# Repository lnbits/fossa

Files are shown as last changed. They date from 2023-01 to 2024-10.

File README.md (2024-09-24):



Welcome to the FOSSA project! FOSSA is an innovative, open-source Bitcoin Lightning ATM designed to be cost-effective and easy to build. Utilizing standard components such as an ESP32 microcontroller, a multi-coin acceptor, and a bill acceptor, FOSSA allows anyone to convert loose fiat change into Bitcoin efficiently. The project includes comprehensive instructions and resources, making it accessible for hobbyists and developers to create a fully functional Bitcoin ATM. Dive in and get started building your own FOSSA!

## Demo

https://twitter.com/arcbtc/status/1567639231333277697

## Bill of Materials

The parts for this ATM should be approximately £200-£250!

You can run the FOSSA as a coin machine, a bill acceptor, or both.

### Primary FOSSA components

| Part | Description | Buy (UK) | Estimated cost |
|---|---|---|---|
| ESP32 WT32-SC01 | This is the ESP32 touchscreen. You don't need any Wi-Fi. It should be supplied with a USB-C to USB cable. Note that the ESP32 WT32-SC01 is different from the ESP32 WT32-SC01 PLUS! | Ebay or [AliExpress](https://www.aliexpress.com/item/1005003191471709.html) | **£45** |
| Option: NV10USB+ bill acceptor | The bill acceptor option to accept cash notes. To accept GBP, you should request that it be set to GBP and SIO mode when purchasing. | [Ebay (second hand)](https://www.ebay.co.uk/itm/263398460026) | **£70-£150** |
| Option: DG600F(S) Multi Coin Acceptor | The coin acceptor option. The "S" denotes the front panel (stainless steel sheet version, where we can 3D print a black panel for it). | [AliExpress](https://www.aliexpress.com/w/wholesale-DG600F(S)-Multi-Coin-Acceptor.html?spm=a2g0o.home.search.0) or eBay | **£30** |
| Screw terminal block | Easily connect the wires without soldering. | [Amazon (UK)](https://www.amazon.co.uk/gp/product/B08LNWMMHQ) | **£1** |
| 12v power supply | Best to get one with terminal block adapter (12v battery also works well, for unplugged version). | [Amazon (UK)](https://www.amazon.co.uk/gp/product/B09MTBTXDJ/) | **£8** |
| 12v to 5v step down converter with USB | 12V to 5V: The adapter converter module can convert unstable voltage DC 12V to stable DC 5V / 15W 3A output. | [Amazon (UK)](https://www.amazon.co.uk/gp/product/B07QQ587K3) | **£5**
| Male-to-female GPIO jumpers | Plug and play GPIO connectors | [Amazon (UK)](https://www.amazon.co.uk/gp/product/B09MJZDXBB) | **£5**
| Option: Aluminum "medicine box" | Cheap medicine box for the cash machine | Amazon (UK) | **£30** |
| Option: Amazon Basic Home Safe | More secure box | Amazon (UK) | **£70** |
| Option: 58mm 701 USB Thermal Receipt Printer | Print receipts for users. **NB The 3D printed enclosure does not currently fit this**. | [Ebay (UK)](https://www.ebay.co.uk/itm/293668439213) | **£25** |



### 3D printed enclosure fixtures & fittings

For the 3D-printed version, you will need:

| Part | Description | Buy (UK) |
|---|---|---|
| M4 x 16mm pan head security torx tamper-resistant bolts | These hold the front facia to the back box. Anything longer than 14mm - 55mm is fine. | [Amazon (UK)](https://www.amazon.co.uk/gp/product/B0BTTRPBQV/) |
| Tamper-proof torx wrench (T20) | To tighten the front facia Torx bolts. | [Amazon (UK)](https://www.amazon.co.uk/gp/product/B0D53LNNRW) |
| Brass insert nuts, M4 x 6mm L x 6mm OD | Female threaded heat set knurled embedded insert nuts for 3D printing. These are stronger than trying to create threads in the 3D print. Using a soldering iron, these are heated up and pushed into the backbox for better attachment of the facia. | [Amazon (UK)](https://www.amazon.co.uk/gp/product/B09MCVW4GQ/) |
| M4 x 30mm carriage/coach bolts | These are to replace the bolts supplied with the coin acceptor to accommodate the thickness of the facia. | [eBay (UK)](https://www.ebay.co.uk/itm/386550912089?var=653926055961) |
| 5.5mm x 2.1mm DC Power Jack Socket Female Panel Mount Connector | This allows the 12V adaptor to plug into the ATM's outside. The box assumes a diameter of 7.7mm (like these). | [Amazon (UK)](https://www.amazon.co.uk/dp/B01N3679B8) |
| 2.2mm Quick Disconnect Female Spade Connector | This allows us to crimp a cable and connect to the 5.5mm x 2.1mm DC Power Jack Socket | |
| Cabinet draw tubular 16mm lock | This will be mounted on the door. | [Amazon (UK)](https://www.amazon.co.uk/Litensh-Tubular-Cylinder-Cupboard-Letterbox/dp/B09SHWXWXC/) |
| Optional: Rubber feet (D30x22xH15) | If you want to have this one on the table, some rubber feet will go at the bottom of the backbox with an M5 bolt. You can also use adhesive versions. Grooves in the bottom of the box will support up to 30mm in diameter. | [Amazon (UK)](https://www.amazon.co.uk/dp/B0CQ23M5Z5) |
| Optional: M5 x 16mm hex socket bolts | To screw the rubber feet into the back box. | [Amazon (UK)](https://www.amazon.co.uk/16mm-Socket-Button-Head-Screws/dp/B09BG8XNM7) |
| Optional: M5 nylon nuts | To screw the rubber feet into the backbox. | [Amazon (UK)](https://www.amazon.co.uk/Bolt-Base-Stainless-Insert-Nylock) |
| Optional: Adhesive security plate and locking cable | Secure the ATM when desk mounted. | [Amazon (UK)](https://www.amazon.co.uk/I3C-Security-Anti-Theft-Hardware-Smartphone/dp/B07FM93JL6) |

## Build

A video tutorial is available here on how to construct the FOSSA:

[https://www.youtube.com/watch?v=vbyYb9Yiu_k](https://www.youtube.com/watch?v=vbyYb9Yiu_k)

### Step 1: Hardware Setup

> **STAY TUNED FOR A WIRING HARNESS TO MAKE THIS PLUG-AND-PLAY, AND YOU CAN SKIP TO STEP 2.**

This method requires no soldering. We do this by using GPIO jumpers and terminal blocks. First, split a terminal block into a block of 3 (our LIVE terminal) and a block of 4 (our GROUND terminal).

The wiring reference is as follows:



**To connect the bill acceptor**:

1. Connect the Rx (GPIO 32) and Tx (GPIO 33), pins 29 and 31, on the WT32-SC01 board to pins 1 and 5, respectively, on the bill acceptor.
2. Using a GPIO jumper, connect the live wire (pin 15) to the first LIVE terminal block at an available terminal.
3. Using a GPIO jumper, connect the ground wire (pin 16) to a second GROUND terminal block of block at an available terminal.
4. Connect the positive wire (red) of the 12V to 5V power converter and connect it to the LIVE terminal block at an available terminal.
5. Connect the negative wire (black) of the 12V to 5V power converter and connect it to the GROUND terminal block at an available terminal.
6. Connect the ground pin (e.g. pin 5) of the WT32-SC01 and connect it to the 2nd terminal of the GROUND terminal block at an available terminal.

| NV10USB+ Pin | WT32-SC01 Pin No. (Not GPIO No.) | Power Supply |
|---|---|---|
| 1 (Tx)  | 31 | N/A |
| 5 (Rx)  | 29 | N/A |
| 15 (12V DC+) | N/A | 12V DC+ |
| 16 (GND) | 5 | GND |

> The bill acceptor needs to be programmed to your currency and set to `SIO` mode. Usually, you can buy them preconfigured. If you have to program, buy <a href="https://www.innovative-technology.com/shop/cables/nv9-nv10-usb-host-cable-detail">this wire</a> and download the Validator Manager software <a href="https://www.dropbox.com/sh/2mle0czl2j2w7yq/AABie6AJQTq-tXmBv1TUhBUGa?dl=0">here</a> or <a href="http://www.innovative-technology.com/support/secure-download">here</a> (sadly only runs on windows, so use a friends machine). Details on programming can be found <a href="https://github.com/arcbtc/fossa/blob/main/NV10Manual_2.PDF.pdf">here</a>. It's relatively straightforward to program the acceptor: plug in the USB host cable, turn it on by holding the config button for 2 seconds, and open the Validator Manager software. If you prefer to build your own programming cable, see page 42 of the <a href="NV10 operations manual.pdf">NV10 USB Operations Manual</a>, which gives a wiring diagram for the NV10 USB host cable. You can ignore all the hardware requirements for programming in the guide; you just need the host cable! Don't try using the programming cards in the guide; that's an old system these machines no longer support - "Many Bothans died to bring us this information"!

**To connect the coin acceptor**:

> NB You can usually order the coin acceptor pre-programmed to your currencies. Otherwise, you will need to train the acceptor using <a href="https://www.youtube.com/watch?v=Dyun1xjKqc4">this guide</a>.

1. Set the 3rd dip switch to high (this sends integers to the WT32-SC01 rather than pulses).
2. Using a GPIO jumper, connect the interrupt pin (pin 5) on the coin accepter to the 5V pin (pin 2) on the WT32-SC01.
3. Using a GPIO jumper, connect the serial out (pin 2) on the coin accepter to pin 4 on the  WT32-SC01.
4. Using a GPIO jumper, connect the live pin (pin 1) to the LIVE terminal block at an available terminal.
5. Using a GPIO jumper, connect the GND pin (pin 3) on the coin accepter to the GROUND terminal block at an available terminal.

| DG600F(S) Pin | WT32-SC01 Pin No. (Not GPIO No.) | Power Supply
| --- | --- | --- |
| 5 | 2 | N/A |
| 4 | N/A | N/A |
| 3 (GND) | N/A | GROUND
| 2 (serial out) | 4 | N/A
| 1 (12V) | N/A | LIVE

**To connect the 12V power supply**:

1. Connect a GPIO jumper to the live connection (+) on the 12V power supply terminal block adapter to the LIVE terminal block at an available terminal.
2. Connect a GPIO jumper to the ground connection (-) on the 12V power supply terminal block adapter to the GROUND terminal block at an available terminal.

**To complete the terminal blocks**:

1. Connect each terminal in the LIVE terminal block so they all receive power by looping over wires from terminals 1 to 2 and 1 to 3.
2. Connect each terminal in the GROUND terminal block so they all receive power by looping over wires from terminals 1 to 2, 1 to 3 and 1 to 4.

**To connect to power**:

1. Plug in the WT32-SC01 to the USB connector of the 12V to 5V power converter.
2. Plug in the connection terminal of the 12V power supply and connect to mains power.

You should hear the bill acceptor and coin acceptors turn on.

### Step 2: Configure LNBits

To configure your LNBits instance to pull funds from:

1. Login to your instance of LNBits.
2. Create a wallet.
3. Go to `Manage Extensions`, find `LNURLDevice`, and install/enable it.
4. Open the `LNURLDevice` extension, click `New LNURLDevice Instance`, give it the title of `ATM`, and choose the appropriate wallet for the ATM. Select the correct currency (e.g., `GBP`), `ATM` mode, and a percentage for the commission.
5. Copy the link it gives you.

### Step 3: Programming the WT32-SC01

The ATM is configured in two parts: the ATM and LNBits running on a separate node.

To set up your Arduino IDE:

1. If you have not already done so, install the Arduino IDE from [https://www.arduino.cc/en/Main/Software](https://www.arduino.cc/en/Main/Software).
2. Install the ESP32 libraries. You can do this by copying the stable release version link, currently `https://espressif.github.io/arduino-esp32/package_esp32_index.json` and putting in the `File` > `Preferences...` > `Additional Board Manager URLs` (see: [https://docs.espressif.com/projects/arduino-esp32/en/latest/installing.html](https://docs.espressif.com/projects/arduino-esp32/en/latest/installing.html))
3. Install the boards by going to `Tools` > `Board` > `Board Manager...`, searching for ESP32, choose 2.0.17, and click Install.
4. Copy the libraries from this project <a href="/libraries">libraries</a> folder to your `"/Arduino/libraries"` folder (usually in OS `"Home"` directory)
5. Clone the repo and open accessPointFOSSA.
6. Select the relevant port and ESP32 dev module.
7. Go to `Sketch` > `Upload`.
8. Once uploaded, the access portal will launch when you press the screen on the WT32-SC01 device.

To configure the ATM:

1. Connect the access portal wi-fi (`Device-fa7ce5a4`, for example).
2. Open the access portal.
2. Enter a new password.
3. Enter the coin denominations (if you are using a coin acceptor, separated by a comma)
4. Enter the maximum withdrawal amount in fiat (e.g. `30` for 30 GBP).
5. Enter a percentage charge for the service (e.g. `10` for 10%, which should be the same value you entered into LNBits).
6. Click `Save`.
7. unplug and plug the WT32-SC01 back in once saved. You should see the `Fiat for Sats` screen.

### Step 4: Enclosure

> It should be pointed out that this ATM is designed to be attended to (such as on a shop counter) rather than something that can be left unattended and mounted to a wall.

#### Option A: 3D printed enclosure

If you want to want to print your own enclosure, we recommend these settings:

1. Print the Facia
    - STL: [FOSSA ATM Facia](https://github.com/lnbits/fossa/blob/main/3DPrints/FOSSA%20ATM%20Facia.stl)
    - Material: PETG
    - Layer: 0.2mm
    - Infill: 10-100% (recommend 20%+)
    - Supports: Yes
    - Notes: To set the Bitcoin logo with a different color, set a color change at layer 114 (13.20mm). In PrucaSlicer, you can "paint" out all the screw holes as they do not need supports. I would also recommend setting a thicker layer parameter, in PrucaSlicer, you can do this by settings `Printer Settings` > `Layers and perimeters` > `Perimeters` to `4`)
3. Print the backbox
    - STL: [FOSSA ATM Backbox](https://github.com/lnbits/fossa/blob/main/3DPrints/FOSSA%20ATM%20Back%20Box.stl)  
    - Material: PETG
    - Layer: 0.2mm 
    - Infill: 10-100% (recommend 20%+)
    - Supports: Yes
    - Notes: In PrusaSlicer you can set `Print Settings` > `Support material` > `First layer expansion` to `1 mm`, `XY separation between an object and its support` to `80%` and `Overhang threshold` to `1 mm`, or, you can "paint" out all but the door as the model has been designed for minimal supports
4. Print the accessories
    - STL: [FOSSA ATM WT-32-SC01 Backplate](https://github.com/lnbits/fossa/blob/main/3DPrints/FOSSA%20ATM%20WT-32-SC01%20Backplate.stl), [FOSSA ATM Coin Slot Cover](https://github.com/lnbits/fossa/blob/main/3DPrints/FOSSA%20ATM%20Coin%20Slot%20Cover.stl), [FOSSA ATM 4mm Lock Lever Shim](https://github.com/lnbits/fossa/blob/main/3DPrints/FOSSA%20ATM%204mm%20Lock%20Lever%20Shim.stl), [FOSSA ATM Door](https://github.com/lnbits/fossa/blob/main/3DPrints/FOSSA%20ATM%204mm%20Door.stl), [FOSSA ATM Backbox Note Holder](https://github.com/lnbits/fossa/blob/main/3DPrints/FOSSA%20ATM%20Backbox%20Note%20Holder.stl)
    - Material: PETG
    - Layer: 0.2mm 
    - Infill: 10-100% (recommend 20%+)
    - Supports: No
5. Use a soldering iron to melt the brass female embedded insert nuts into the six holes for the facia (see picture 1 below)
6. OPTIONAL: If using the coin acceptor, replace the coach bolts with longer bolts (M4 x 30mm carriage/coach bolts) to account for the thickness of the facia.
7. Mount the bill acceptor so it is "smiling" (see picture 2) with the supplied mounting bracket and screws as pictured (see picture 3). You can remove the bill input feed from the main part of the unit and then re-attach it.
8. Mount the screen to the WT-32-SC01 Backplate.
9. Mount the backplate to the Facia with the M4 (4mm x 8mm Inc Head) hex socket countersunk screws.
10. Mount the backbox note holder to the backbox with the M4 (4mm x 8mm Inc Head) hex socket countersunk screws.
11. Mount the 5.5mm x 2.1mm DC Power Jack Socket Female Panel Mount Connector in the hole in the back left of the backbox (this directs the notes to the bottom of the box.
12. Connect wires from the connection terminal to the 2.2mm Quick Disconnect Female Spade Connector and plug into the inside of the 5.5mm x 2.1mm DC Power Jack Socket Female Panel Mount Connector.
13. OPTIONAL: Mount the Rubber feet (D30x22xH15) using the M5 x 16mm hex socket bolts and M5 nylon nuts (be careful not to over-tighten).
14. Using the Tamper-proof torx wrench (T20), use the screw in the M4 x 16mm pan head security torx tamper-resistant bolts to secure the facia to the backbox.
15. Plug the power supply in.





#### Option B: Mount in a box

Use the templates provided <a href="cuttingTemplate.pdf">here</a>, print out at 100% on standard UK A4, and check the dimensions are correct after printing. It's helpful if the bill acceptor and coin mech pins are accessible.

* For the `Aluminium Storage Box` solution, holes can be cut with a sharp knife (clearly not secure - but acceptable for somewhere you can keep an eye on the ATM or for demos).

* For the `Home Safe` solution, holes can be cut with an angle grinder and a very thin cutter. (If you have not used an angle grinder before, don't be scared; they're cheap, easy enough to use, and very useful. Take your time and wear safety equipment.)

> We use CT1 sealant/adhesive (or similar) for mounting the screen, although the screen has screw points, which should prob be used for added security.

## Get in touch

And there you have it. Have fun, and tag us on Twitter / Nostr with all your cool setups!

> <i>Join our <a href="https://t.me/makerbits">telegram support/chat</a>.</i>

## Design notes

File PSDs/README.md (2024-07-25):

## PhotoShop Files

### FOSSA - The FOSS ATM

This is the heading image for the repo.

### FOSSA - Primary components

Overview visual of the main components used.

### FOSSA - Primary wiring reference

Wiring and pin labelling for the main components.

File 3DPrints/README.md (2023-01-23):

##### Few people have used a case for the WT32, this does however add the security risk that people have access to the USB. A flush finish and not using a case is advised, but we thought we'd share anyway.

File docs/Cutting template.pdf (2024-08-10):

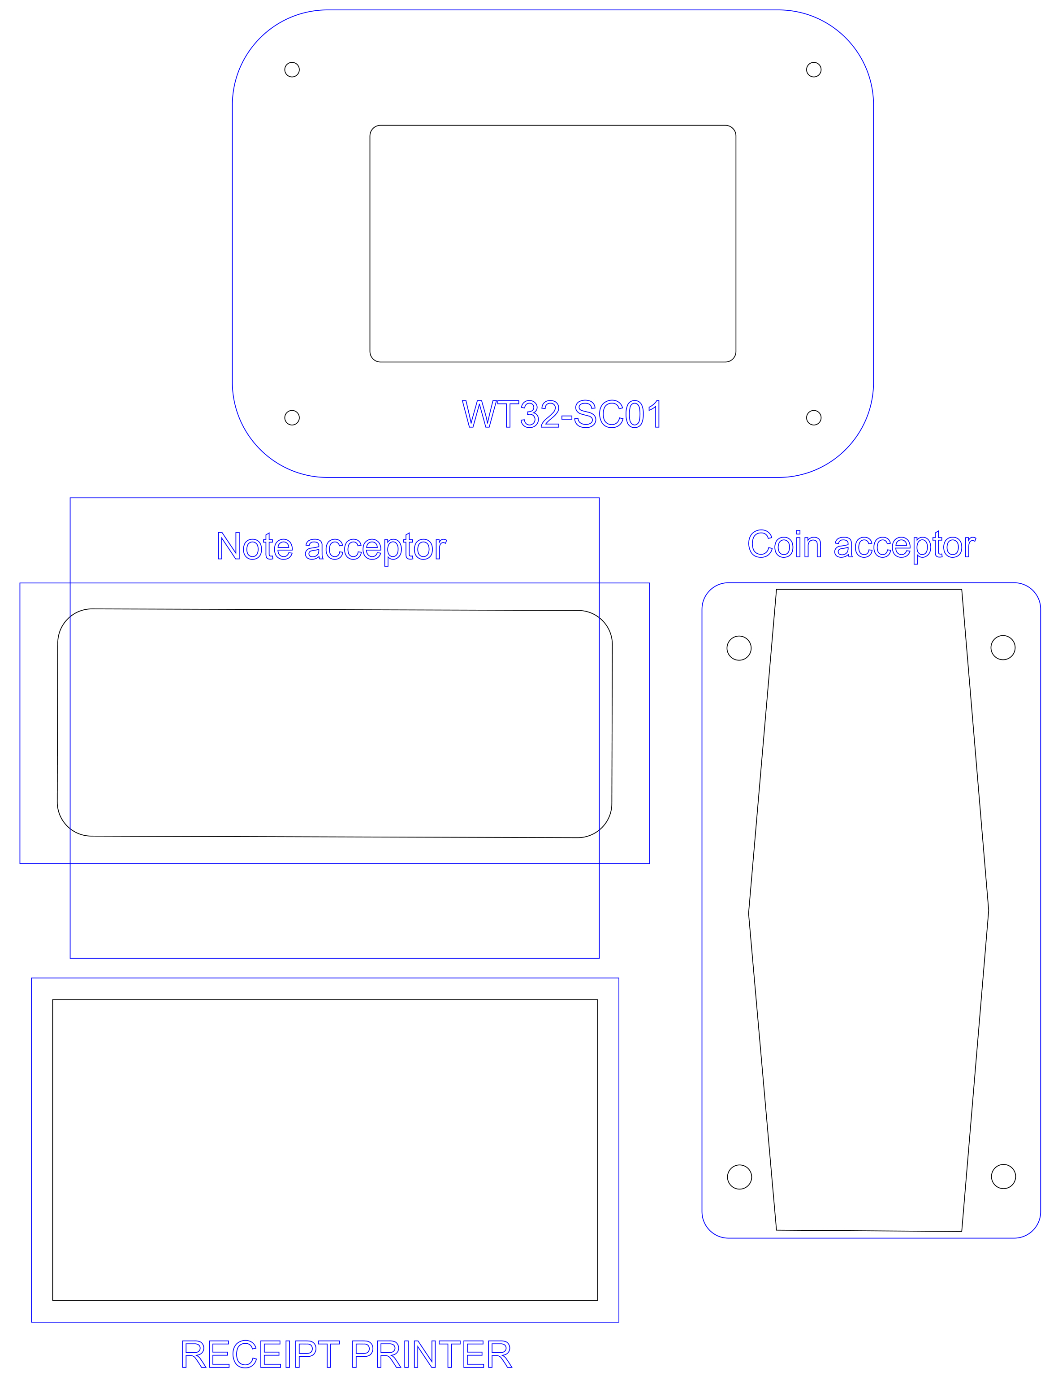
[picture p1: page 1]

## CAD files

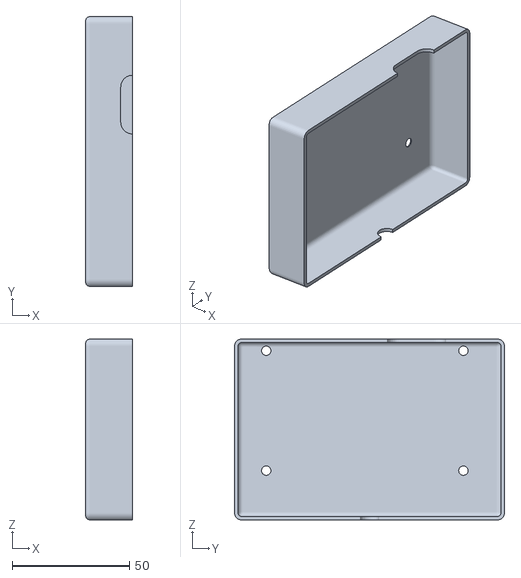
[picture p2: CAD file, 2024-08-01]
3DPrints/FOSSA ATM LNBits Board Cover.stl
20.0 x 114.9 x 77.0

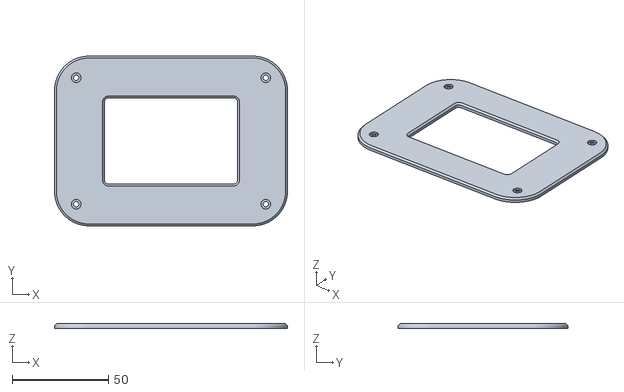
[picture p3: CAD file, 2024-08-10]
stls/WT32-SC01 enclosure upper.stl
121.2 x 88.3 x 2.50

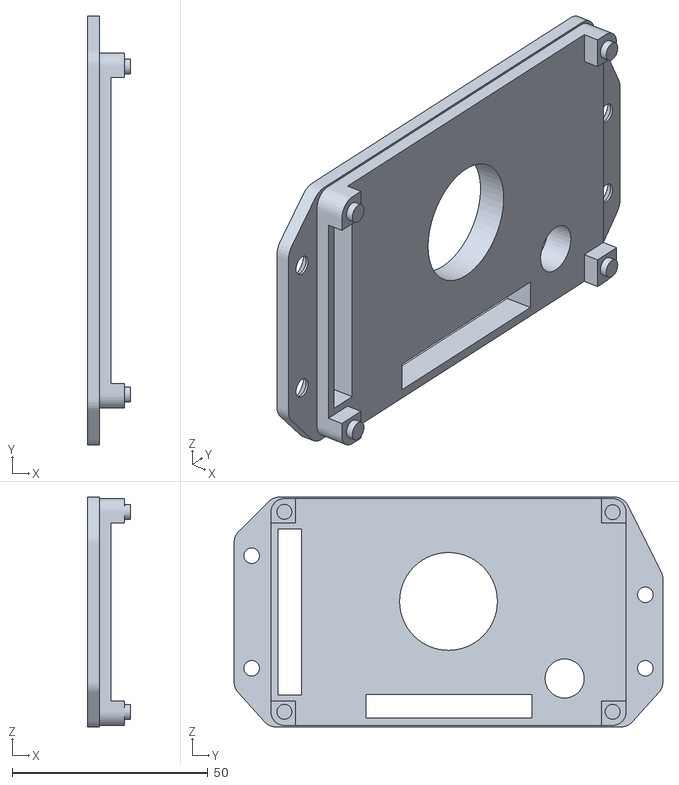
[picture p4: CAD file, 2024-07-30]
3DPrints/FOSSA ATM WT32-SC01 Backplate.stl
10.9 x 109.7 x 58.8

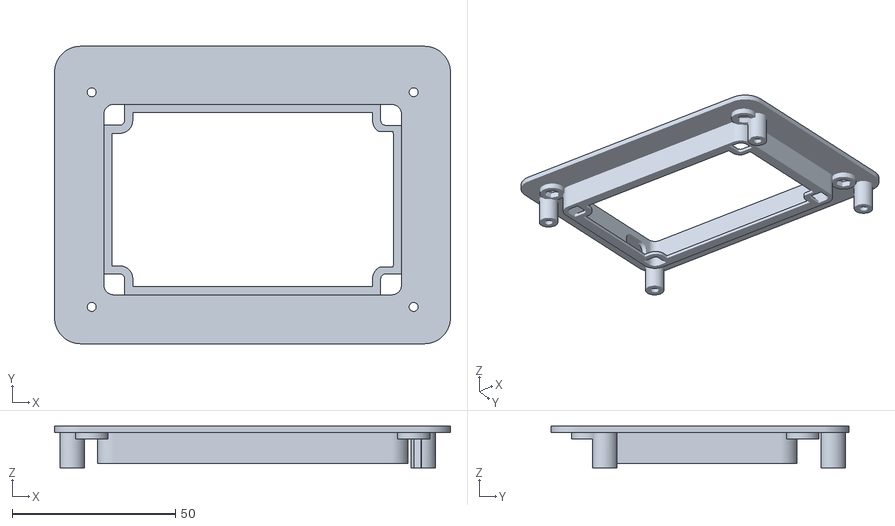
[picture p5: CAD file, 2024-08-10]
stls/WT32-SC01 enclosure lower.stl
121.3 x 91.1 x 12.8

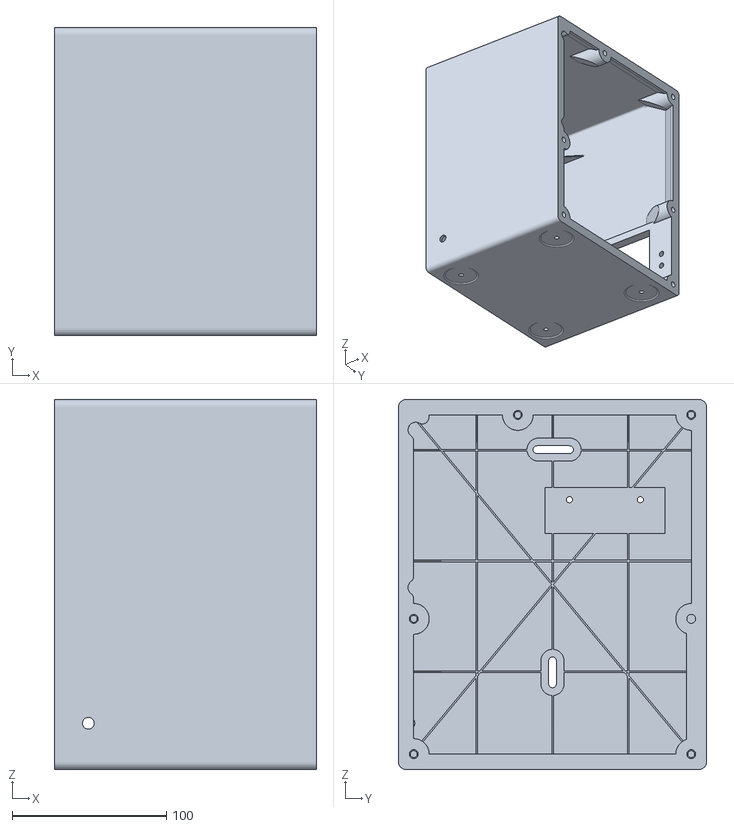
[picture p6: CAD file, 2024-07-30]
3DPrints/FOSSA ATM Backbox.stl
170.0 x 200.0 x 240.0

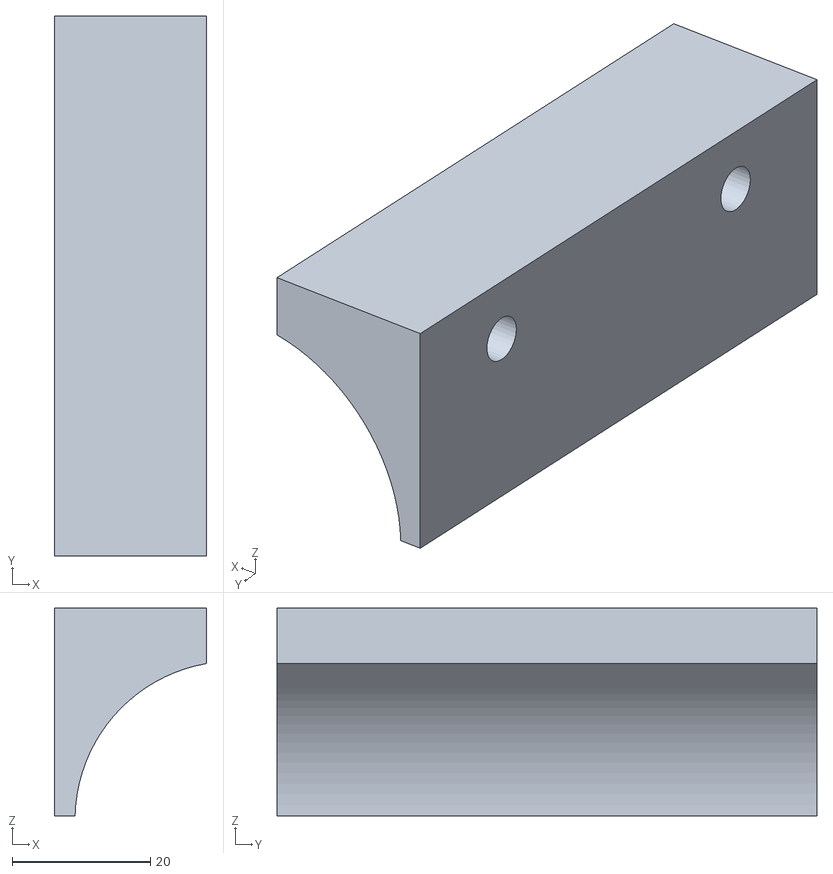
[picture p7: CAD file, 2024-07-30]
3DPrints/FOSSA ATM Backbox Note Holder.stl
22.0 x 78.0 x 30.0

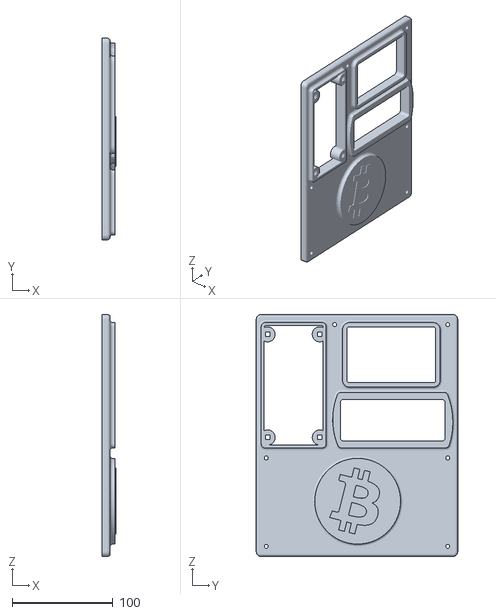
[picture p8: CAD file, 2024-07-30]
3DPrints/FOSSA ATM Front Facia.stl
13.8 x 200.0 x 240.0

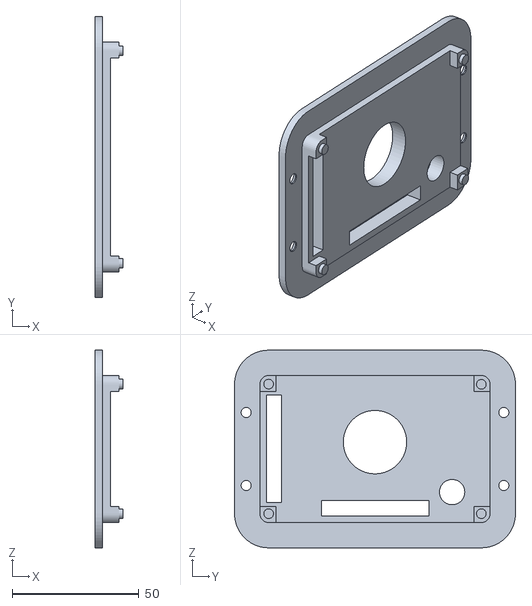
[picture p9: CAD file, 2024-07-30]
3DPrints/FOSSA ATM Screen Backplate.stl
10.9 x 110.9 x 78.0

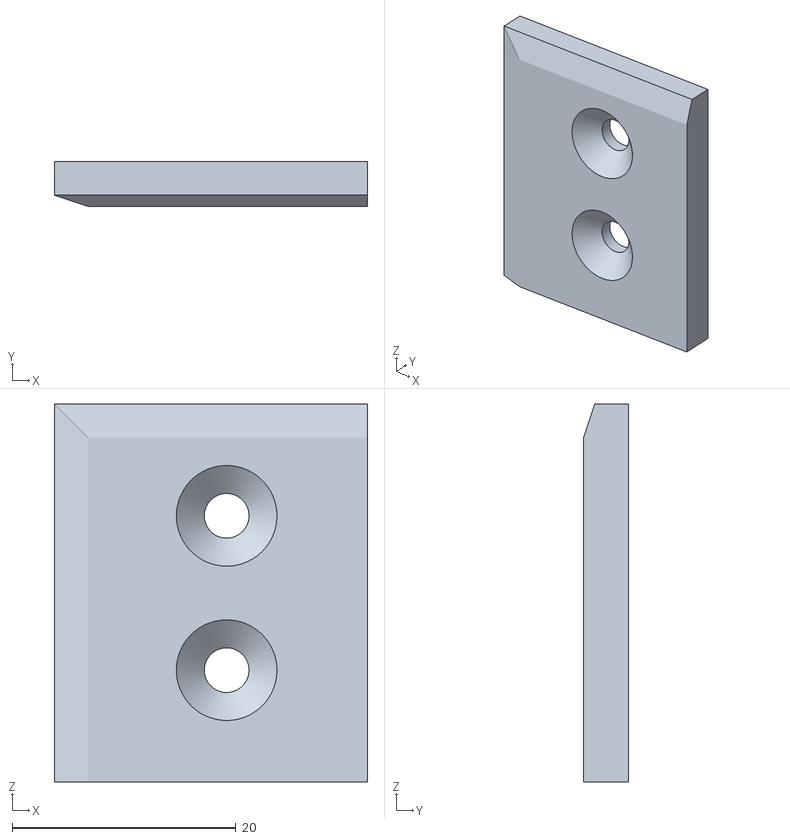
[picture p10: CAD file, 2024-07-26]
3DPrints/FOSSA ATM 4mm Lock Lever Shim.stl
28.0 x 4.00 x 33.8

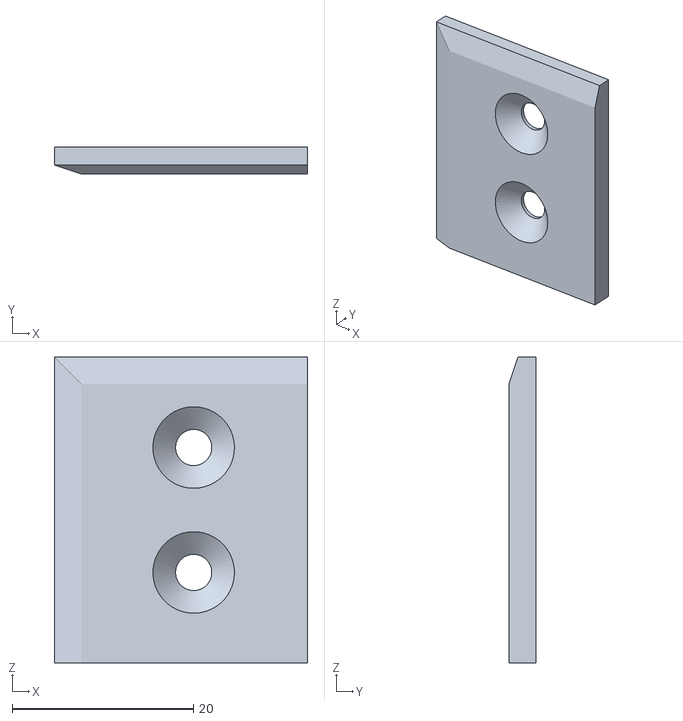
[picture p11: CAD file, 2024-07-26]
3DPrints/FOSSA ATM 3mm Lock Lever Shim.stl
28.0 x 3.00 x 33.8

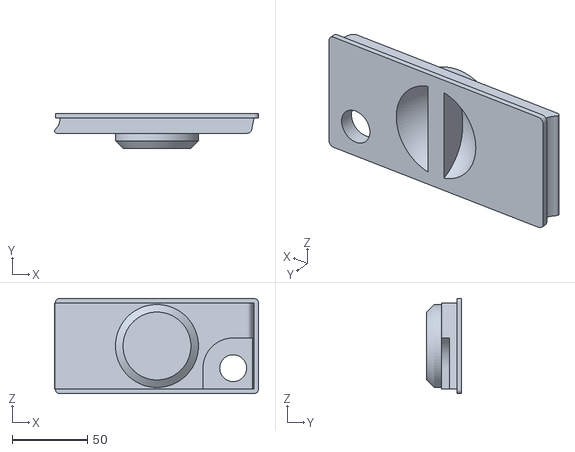
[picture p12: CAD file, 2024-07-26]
3DPrints/FOSSA ATM Door.stl
135.2 x 23.0 x 63.0

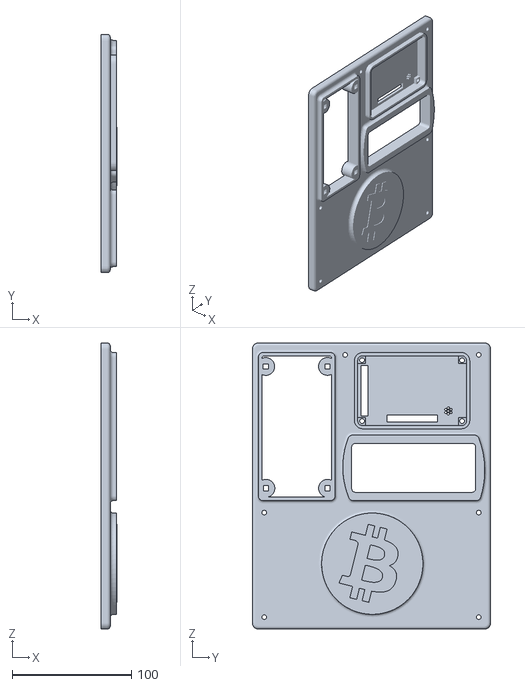
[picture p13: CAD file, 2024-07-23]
3DPrints/FOSSA ATM Facia.stl
13.8 x 200.0 x 240.0

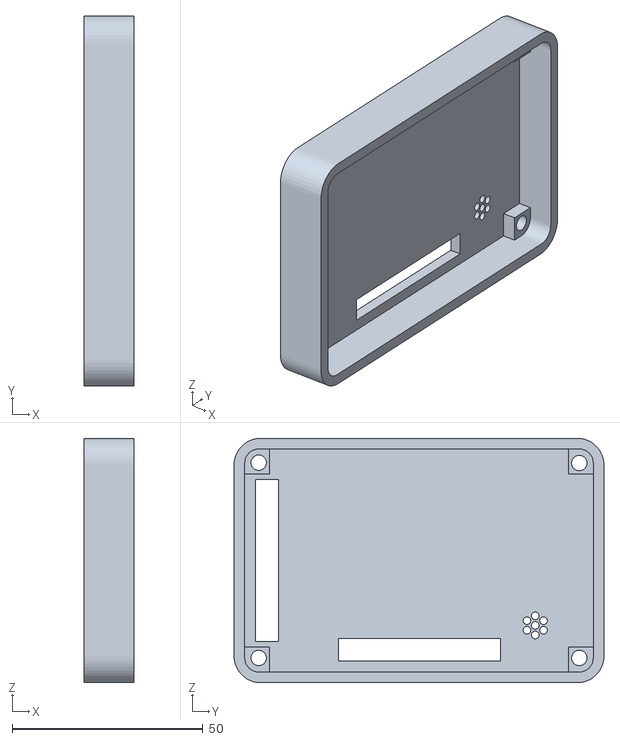
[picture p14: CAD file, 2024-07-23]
3DPrints/FOSSA ATM Screen Mount Test.stl
13.0 x 96.9 x 64.0

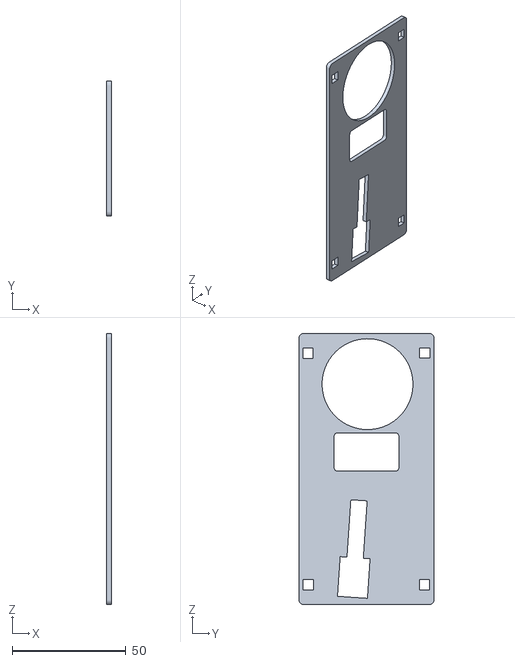
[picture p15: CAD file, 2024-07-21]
3DPrints/FOSSA ATM Slot Cover.stl
2.00 x 59.5 x 119.3

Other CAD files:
3DPrints/WT32-SC01 Case.stl
3DPrints/FOSSA ATM Back Box.stl

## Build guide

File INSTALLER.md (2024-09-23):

<h1>
FOSSA! Free and Open Source ATM
</h1>
<h3>NOW SUPPORTS ONCHAIN AND LIQUID PAYOUTS!!! (powered by magical sub-atomic trustless swaps!)</h3>

## Free and open-source bitcoin point-of-sale

Fossa includes:

FOSSA is a popular cheap DIY bitcoin ATM with many forks.
<br></br>
FOSSA is offline, and can be used with a bill acceptor, coin acceptor or both! FOSSA supports a thermal printer, and can pay out in bitcoin on lightning, onchain or liquid (using the magic of trustless swaps, no onchain or liquid hotwallet needed!!!) 
  <br></br>
  HUGE thanks to all contributors and users, especially BlackCoffee and Ben Weeks!

Join our telegram group <a href="https://t.me/makerbits">MakerBits</a>

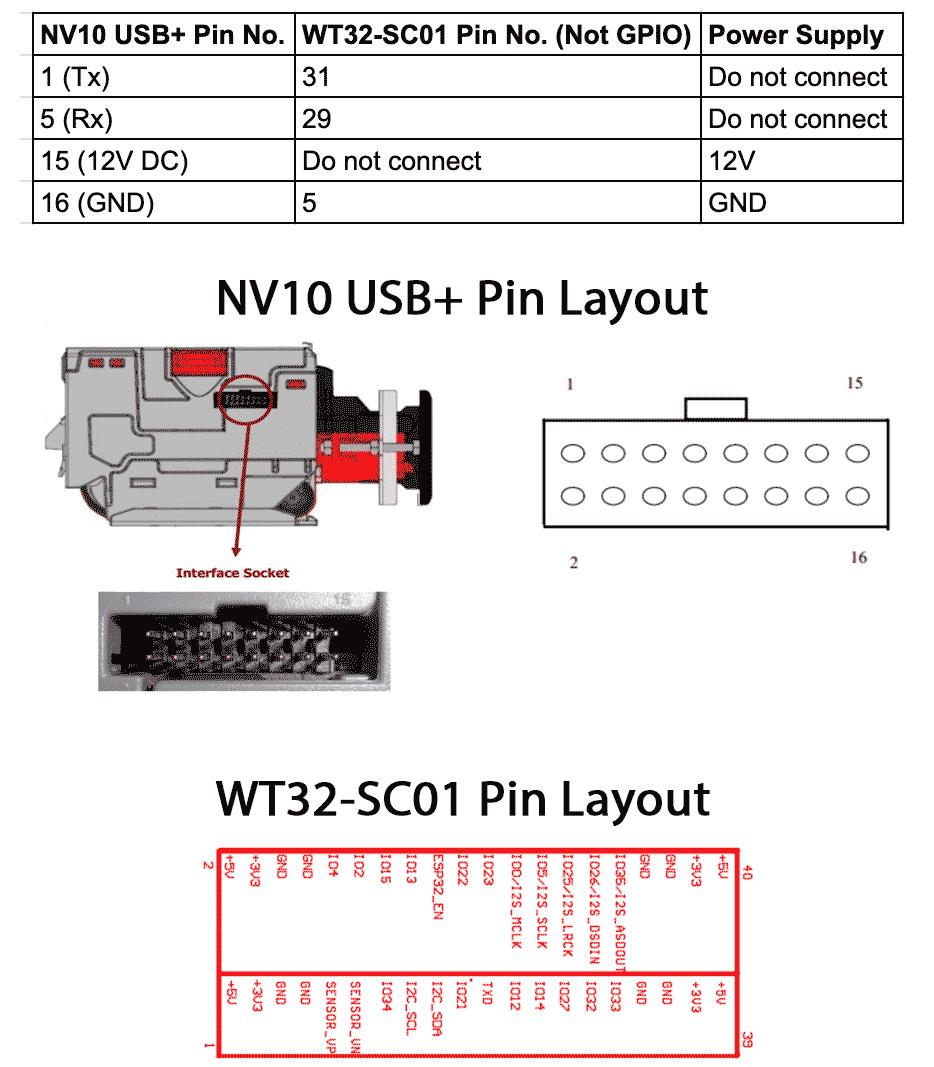
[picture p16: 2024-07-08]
img/nv10-wiring.png

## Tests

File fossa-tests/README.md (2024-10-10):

# Bare-bones useful tests

For debugging whether you can talk to the bill acceptor, coin acceptor and printer.

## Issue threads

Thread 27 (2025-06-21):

BUG: After inserting coins it prints WARNING: print bool

bitcointwente, 2025-06-21:
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

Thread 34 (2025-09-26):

BUG: Unexpected error! ID: .. and Invalid payload length.

AxelHamburch, 2025-09-26:
The Fossa extension with LNbits v1.2 works wonderfully. I have now used the test server v1.lnbits.com to test version v1.3.0rc8. After setting up an instance and configuring the ATM with it, the wallets display the error “Invalid payload length.”

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

In LNbits, I noticed that I get an error message when I call up the Fossa extension. Here are two different instances:

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

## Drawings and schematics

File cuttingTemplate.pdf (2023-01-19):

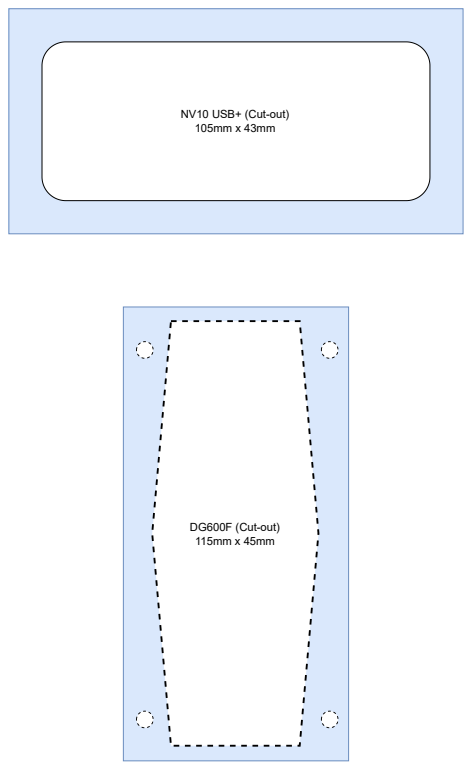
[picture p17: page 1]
DG600F (Cut-out) 115mm x 45mm

NV10 USB+ (Cut-out)

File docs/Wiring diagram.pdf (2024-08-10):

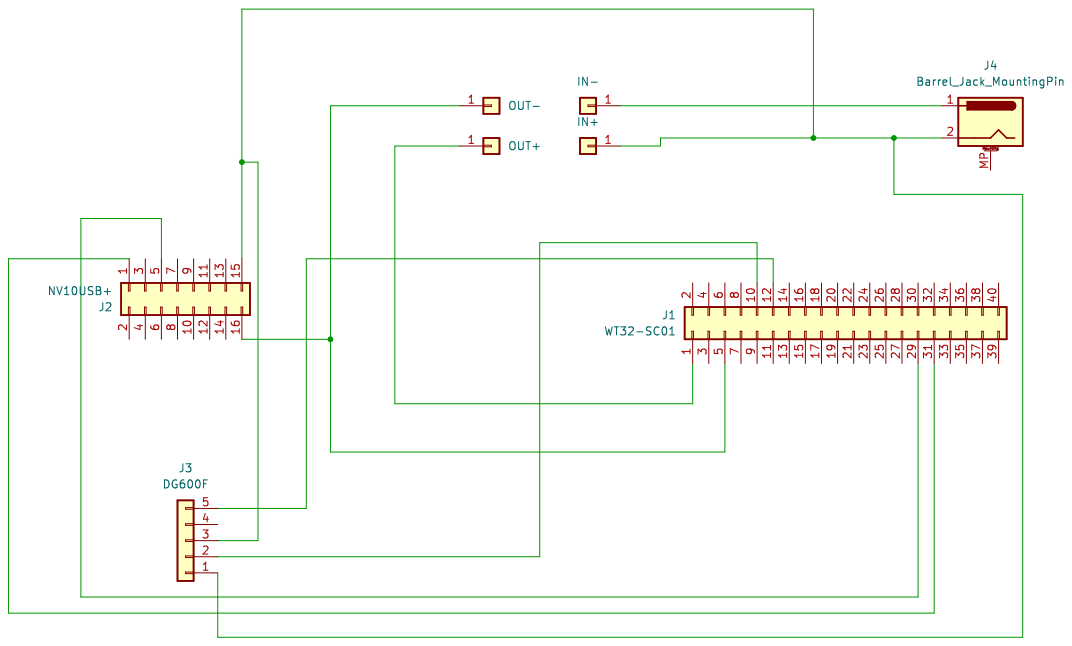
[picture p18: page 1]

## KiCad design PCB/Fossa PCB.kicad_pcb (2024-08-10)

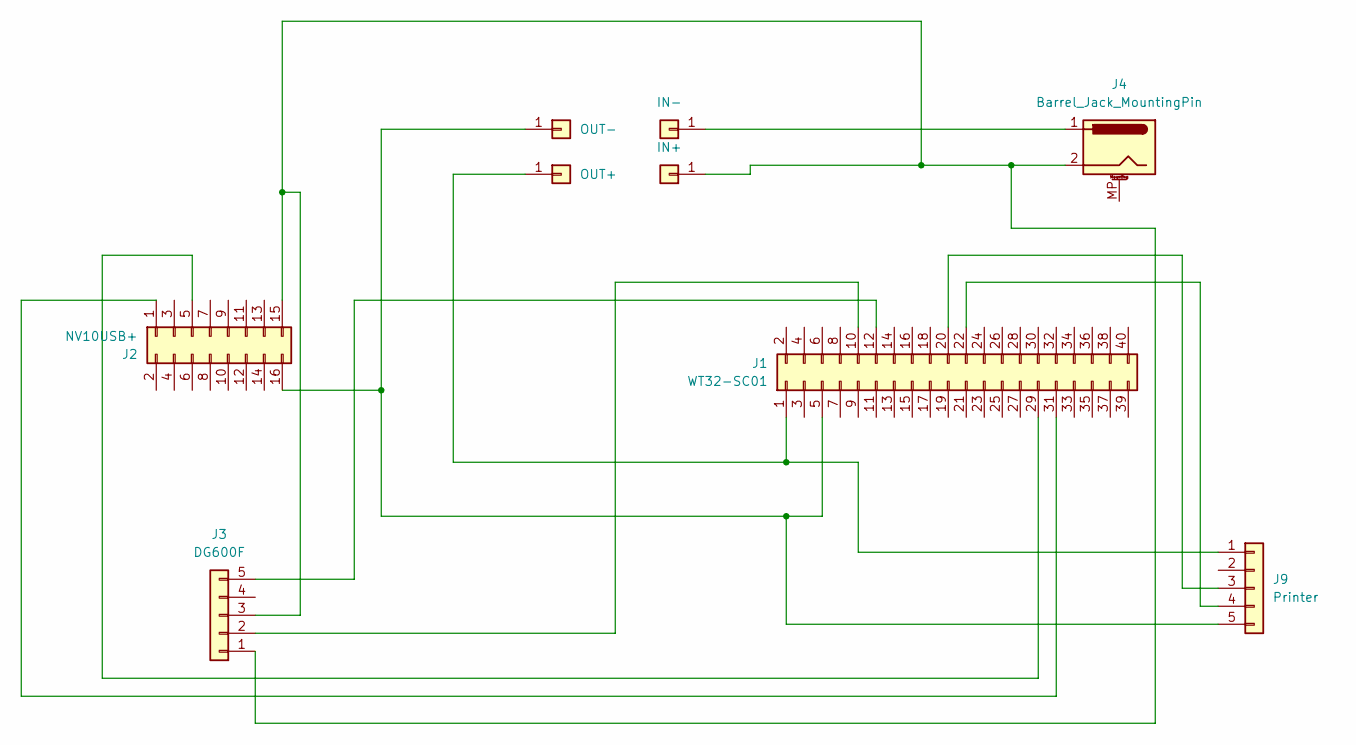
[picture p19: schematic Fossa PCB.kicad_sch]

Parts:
J1: WT32-SC01; PinHeader_2x20_P2.00mm_Vertical
J2: NV10USB+; PinHeader_2x08_P2.54mm_Vertical
J3: DG600F; PinHeader_1x05_P2.54mm_Vertical
J4: Barrel_Jack_MountingPin; BarrelJack_CUI_PJ-063AH_Horizontal
J5: IN+; PinHeader_1x01_P2.54mm_Vertical
J6: IN-; PinHeader_1x01_P2.54mm_Vertical
J7: OUT+; PinHeader_1x01_P2.54mm_Vertical
J8: OUT-; PinHeader_1x01_P2.54mm_Vertical
J9: Printer; PinHeader_1x05_P2.54mm_Vertical

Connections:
unnamed: J1.1, J7.1, J9.1
unnamed: J1.5, J2.16, J8.1, J9.5
unnamed: J1.10, J3.2
unnamed: J1.12, J3.5
unnamed: J1.20, J9.3
unnamed: J1.22, J9.4
unnamed: J1.29, J2.5
unnamed: J1.31, J2.1
unnamed: J2.15, J3.1, J3.3, J4.2, J5.1
unnamed: J4.1, J6.1

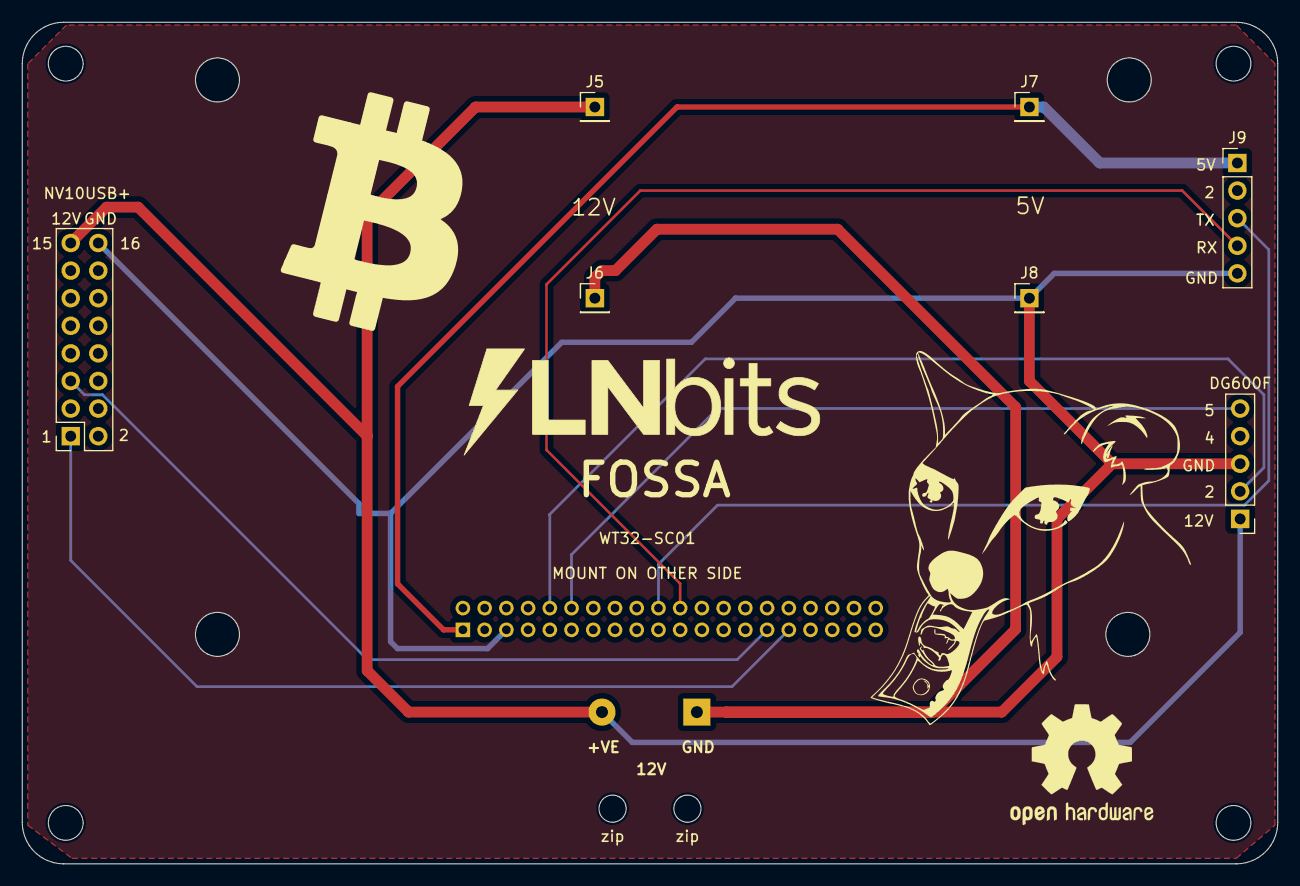
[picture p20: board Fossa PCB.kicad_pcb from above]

Board: 2 copper layers, 115.6 x 77.5 mm, 11 parts (1 on the bottom side), 10 nets.

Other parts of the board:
zip: zip; MountingHole_2.5mm
zip#2: zip; MountingHole_2.5mm

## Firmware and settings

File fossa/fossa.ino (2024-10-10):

#include <Wire.h>
#include <FS.h>
#include <SPIFFS.h>
#include <SoftwareSerial.h>
#include <TFT_eSPI.h>
#include <HardwareSerial.h>
#include <JC_Button.h>
#include <Hash.h>
#include <ArduinoJson.h>
#include "qrcoded.h"
#include "Bitcoin.h"
#include <Adafruit_Thermal.h>
#include <cstdlib>
#define FORMAT_ON_FAIL true
#define PARAM_FILE "/elements.json"

///////////////////////////////////////////////////
//////CHANGE MANUALLY OR USE FOSSA.lnbits.com//////
///////////////////////////////////////////////////

bool hardcoded = false;
String LNURLsettings = "https://lnbits.serveo.net/lnurldevice/api/v1/lnurl/DGB8h,iiPo9beZuTSaFY5smcLhgi,USD";
int billAmountInt[16];
float coinAmountFloat[6];
int charge = 10;          // % you will charge people for service, set in LNbits extension
int maxamount = 30;       // max amount per withdraw
int maxBeforeReset = 300;  // max amount you want to sell in the atm before having to reset power
bool printerBool = false;
String language = "en";  // Supports en, es, fr, de, it, pt, pl, hu, tr, ro, fi, sv

///////////////////////////////////////////////////
///////////////////////////////////////////////////
///////////////////////////////////////////////////

String baseURLATM;
String secretATM;
String currencyATM;

#define BTN1 39        // Screen tap button
#define RX1 32         // Bill acceptor
#define TX1 33         // Bill acceptor
#define TX2 4          // Coinmech
#define INHIBITMECH 2  // Coinmech
#define RXP 22         // TX of the thermal printer
#define TXP 23         // RX of the thermal printer

fs::SPIFFSFS &FlashFS = SPIFFS;

String qrData;

int maxBeforeResetTally;
int bills;
float coins;
float total;
int billAmountSize = sizeof(billAmountInt) / sizeof(int);
float coinAmountSize = sizeof(coinAmountFloat) / sizeof(float);
int moneyTimer = 0;
bool waitForTap = true;
struct KeyValue {
  String key;
  String value;
};
String translate(String key);
uint16_t homeScreenColors[] = { TFT_GREEN, TFT_BLUE, TFT_ORANGE };
int homeScreenNumColors = sizeof(homeScreenColors) / sizeof(homeScreenColors[0]);
int homeScreenNumColorCount = 0;

String usbT, tapScreenT, scanMeT, totalT, fossaT, satsT, forT, fiatT, feedT, chargeT, printingT, waitT, workingT, thisVoucherT, ofBitcoinT, thankYouT, scanMeClaimT, tooMuchFiatT, contactOwnerT;

HardwareSerial SerialPort1(1);
HardwareSerial SerialPort2(2);
SoftwareSerial printerSerial(RXP, TXP);
Adafruit_Thermal printer(&printerSerial);
TFT_eSPI tft = TFT_eSPI(320, 480);
Button BTNA(BTN1);

void setup() {
  translateAll(language);
  Serial.begin(115200);
  Serial.println(workingT);
  BTNA.begin();
  FlashFS.begin(FORMAT_ON_FAIL);
  tft.init();
  tft.setRotation(1);
  tft.invertDisplay(false);
  printMessage("", "Loading..", "", TFT_WHITE, TFT_BLACK);

  // wait few secods for tap to start config mode
  while (waitForTap && total < 100 && hardcoded == false) {
    BTNA.read();
    if (BTNA.wasReleased()) {
      printMessage(usbT, "", tapScreenT, TFT_WHITE, TFT_BLACK);
      executeConfig();
      waitForTap = false;
    }
    delay(20);
    total++;
  }
  
  if(hardcoded == false){
    readFiles();
    translateAll(language);
  }
  splitSettings(LNURLsettings);

  // initialize bill and coin acceptor
  SerialPort1.begin(300, SERIAL_8N2, TX1, RX1);
  SerialPort2.begin(4800, SERIAL_8N1, TX2);
  pinMode(INHIBITMECH, OUTPUT);

  // initialize printer
  if(printerBool == true){
    printerSerial.begin(9600);
    printer.begin();
  }
}

void loop() {
  if (maxBeforeResetTally >= maxBeforeReset) {
    printMessage("", tooMuchFiatT, contactOwnerT, TFT_WHITE, TFT_BLACK);
    delay(100000000);
  } else {
    SerialPort1.write(184);
    digitalWrite(INHIBITMECH, HIGH);
    tft.fillScreen(TFT_BLACK);
    BTNA.read(); // needed to clear accidental taps
    moneyTimerFun();
    Serial.println(total);
    Serial.println(maxBeforeResetTally);
    maxBeforeResetTally = maxBeforeResetTally + (total / 100);
    Serial.println(maxBeforeResetTally);
    makeLNURL();
    qrShowCodeLNURL(scanMeT);
  }
}

void moneyTimerFun() {
  waitForTap = true;
  coins = 0;
  bills = 0;
  total = 0;
  while (waitForTap || total == 0) {
    if (homeScreenNumColorCount == homeScreenNumColors) {
      homeScreenNumColorCount = 0;
    }
    if (total == 0) {
      feedmefiat();
      feedmefiatloop();
    }
    if (SerialPort1.available()) {
      int x = SerialPort1.read();

      for (int i = 0; i < billAmountSize; i++) {
        if ((i + 1) == x) {
          bills = bills + billAmountInt[i];
          total = (coins + bills);
          printMessage(billAmountInt[i] + currencyATM, totalT + String(total) + currencyATM, tapScreenT, TFT_WHITE, TFT_BLACK);
        }
      }
    }
    if (SerialPort2.available()) {
      int x = SerialPort2.read();
        for (int i = 0; i < coinAmountSize; i++) {
          if ((i + 1) == x) {
            coins = coins + coinAmountFloat[i];
            total = (coins + bills);
            printMessage(coinAmountFloat[i] + currencyATM, totalT + String(total) + currencyATM, tapScreenT, TFT_WHITE, TFT_BLACK);
          }
        }
    }
    BTNA.read();
    if (BTNA.wasReleased() || total > maxamount) {
      waitForTap = false;
    }
    homeScreenNumColorCount++;
  }
  total = (coins + bills) * 100;

  // Turn off machines
  SerialPort1.write(185);
  digitalWrite(INHIBITMECH, LOW);
}

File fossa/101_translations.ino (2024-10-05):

// Supports en, es, fr, de, it, pt, pl, hu, tr, ro, fi, sv
String translate(String key, String language) {
  const char* translations = R"(
[en]
usbT = USB config mode
tapScreenT = TAP SCREEN WHEN FINISHED
scanMeT = SCAN ME TAP SCREEN WHEN FINISHED
totalT = Total: 
fossaT = FOSSA! Bitcoin ATM
satsT = SATS
forT = FOR
fiatT = FIAT!
feedT = feed me fiat.
chargeT = % charge
printingT = Printing
waitT = please wait
workingT = Working...
thisVoucherT = This voucher can be redeemed for
ofBitcoinT = of Bitcoin
thankYouT = Thank you
scanMeClaimT = Scan me with a Lightning wallet to get your Bitcoin
tooMuchFiatT = Too much FIAT!
contactOwnerT = Please contact owner
failedT = FAILED
unableT = unable to read lnurl
maxaT = WARNING: max amount
willT = Will use default
loadT = WARNING: load charge
maxrT = WARNING: max reset
printY = WARNING: print bool
langT = WARNING: lang fail

[es]
usbT = Modo de configuracion USB
tapScreenT = TOQUE LA PANTALLA CUANDO TERMINE
scanMeT = ESCANEME TOQUE LA PANTALLA CUANDO TERMINE
totalT = Total:
fossaT = FOSSA! Cajero Bitcoin
satsT = SATS
forT = PARA
fiatT = FIAT!
feedT = dame fiat.
chargeT = % de carga
printingT = Imprimiendo
waitT = por favor espera
workingT = Trabajando...
thisVoucherT = Este vale se puede canjear por
ofBitcoinT = de Bitcoin
thankYouT = Gracias
scanMeClaimT = Escaneame con una billetera Lightning para recibir tu Bitcoin
tooMuchFiatT = Demasiado FIAT!
contactOwnerT = Por favor contacta al propietario
failedT = FALLIDO
unableT = no se puede leer lnurl
maxaT = ADVERTENCIA: cantidad maxima
willT = Usara el valor predeterminado
loadT = ADVERTENCIA: carga de valor
maxrT = ADVERTENCIA: reinicio maximo
printY = ADVERTENCIA: bool de impresion
langT = ADVERTENCIA: error de idioma

[fr]
usbT = Mode de configuration USB
tapScreenT = TOUCHEZ L ECRAN QUAND TERMINE
scanMeT = SCANEZ MOI TOUCHEZ L ECRAN QUAND TERMINE
totalT = Total:
fossaT = FOSSA! Distributeur Bitcoin
satsT = SATS
forT = POUR
fiatT = FIAT!
feedT = nourrissez moi de fiat
chargeT = % charge
printingT = Impression
waitT = veuillez patienter
workingT = En cours...
thisVoucherT = Ce bon peut etre echange contre
ofBitcoinT = de Bitcoin
thankYouT = Merci
scanMeClaimT = Scannez moi avec un portefeuille Lightning pour obtenir votre Bitcoin
tooMuchFiatT = Trop de FIAT !
contactOwnerT = Veuillez contacter le proprietaire
failedT = ECHOUE
unableT = impossible de lire lnurl
maxaT = AVERTISSEMENT: montant maximal
willT = Utilisera la valeur par defaut
loadT = AVERTISSEMENT: charge de chargement
maxrT = AVERTISSEMENT: reinitialisation maximale
printY = AVERTISSEMENT: bool impression
langT = AVERTISSEMENT: echec de langue

[de]
usbT = USB-Konfigurationsmodus
tapScreenT = BERUEHREN SIE DEN BILDSCHIRM WENN FERTIG
scanMeT = SCANNEN SIE MICH BERUEHREN SIE DEN BILDSCHIRM WENN FERTIG
totalT = Gesamt:
fossaT = FOSSA! Bitcoin-Geldautomat
satsT = SATS
forT = FUER
fiatT = FIAT!
feedT = fuettere mich mit Fiat
chargeT = % Ladung
printingT = Drucken
waitT = bitte warten
workingT = Arbeitet...
thisVoucherT = Dieser Gutschein kann eingeloest werden fuer
ofBitcoinT = von Bitcoin
thankYouT = Danke
scanMeClaimT = Scannen Sie mich mit einem Lightning Wallet um Ihr Bitcoin zu erhalten
tooMuchFiatT = Zu viel FIAT!
contactOwnerT = Bitte kontaktieren Sie den Besitzer
failedT = FEHLGESCHLAGEN
unableT = lnurl konnte nicht gelesen werden
maxaT = WARNUNG: Maximalbetrag
willT = Standard wird verwendet
loadT = WARNUNG: Ladefracht
maxrT = WARNUNG: Maximales Zuruecksetzen
printY = WARNUNG: Druck bool
langT = WARNUNG: Sprachfehler

[it]
usbT = Modalita di configurazione USB
tapScreenT = TOCCA LO SCHERMO QUANDO FINITO
scanMeT = SCANSIONAMI TOCCA LO SCHERMO QUANDO FINITO
totalT = Totale:
fossaT = FOSSA! Bancomat Bitcoin
satsT = SATS
forT = PER
fiatT = FIAT!
feedT = dammelo in fiat
chargeT = % carica
printingT = Stampa in corso
waitT = attendere prego
workingT = Funzionamento...
thisVoucherT = Questo voucher puo essere riscattato per
ofBitcoinT = di Bitcoin
thankYouT = Grazie
scanMeClaimT = Scansionami con un portafoglio Lightning per ottenere il tuo Bitcoin
tooMuchFiatT = Troppo FIAT!
contactOwnerT = Per favore contatta il proprietario
failedT = FALLITO
unableT = impossibile leggere lnurl
maxaT = AVVERTENZA: importo massimo
willT = Verra utilizzato il valore predefinito
loadT = AVVERTENZA: carica di carico
maxrT = AVVERTENZA: ripristino massimo
printY = AVVERTENZA: stampa bool
langT = AVVERTENZA: errore di lingua

[pt]
usbT = Modo de configuracao USB
tapScreenT = TOQUE NA TELA QUANDO TERMINAR
scanMeT = ESCANEIE ME TOQUE NA TELA QUANDO TERMINAR
totalT = Total:
fossaT = FOSSA! Caixa eletronico Bitcoin
satsT = SATS
forT = PARA
fiatT = FIAT!
feedT = me de fiat
chargeT = % de carga
printingT = Imprimindo
waitT = por favor aguarde
workingT = Trabalhando...
thisVoucherT = Este voucher pode ser resgatado por
ofBitcoinT = de Bitcoin
thankYouT = Obrigado
scanMeClaimT = Escaneie me com uma carteira Lightning para obter seu Bitcoin
tooMuchFiatT = Muito FIAT!
contactOwnerT = Por favor entre em contato com o proprietario
failedT = FALHOU
unableT = incapaz de ler lnurl
maxaT = AVISO: valor maximo
willT = Usara o valor padrao
loadT = AVISO: carga de valor
maxrT = AVISO: redefinicao maxima
printY = AVISO: bool de impressao
langT = AVISO: falha no idioma

[pl]
usbT = Tryb konfiguracji USB
tapScreenT = DOTKNIJ EKRAN PO UKONCZENIU
scanMeT = SCANUJ MNIE DOTKNIJ EKRAN PO UKONCZENIU
totalT = Razem:
fossaT = FOSSA! Bankomat Bitcoin
satsT = SATS
forT = DLA
fiatT = FIAT!
feedT = daj mi fiat
chargeT = % ladunku
printingT = Drukowanie
waitT = prosze czekac
workingT = Pracuje...
thisVoucherT = Ten bon moze byc wymieniony na
ofBitcoinT = Bitcoin
thankYouT = Dziekuje
scanMeClaimT = Zeskanuj mnie portfelem Lightning aby otrzymac swoj Bitcoin
tooMuchFiatT = Za duzo FIAT!
contactOwnerT = Prosze skontaktowac sie z wlascicielem
failedT = NIEUDANE
unableT = nie mozna odczytac lnurl
maxaT = OSTRZEZENIE: maksymalna kwota
willT = Zostanie uzyta wartosc domyslna
loadT = OSTRZEZENIE: ladunek
maxrT = OSTRZEZENIE: maksymalne zresetowanie
printY = OSTRZEZENIE: bool drukowania
langT = OSTRZEZENIE: blad jezyka

[hu]
usbT = USB konfiguracios mod
tapScreenT = TAP IN EKRANRA HA VEGE
scanMeT = SZKENNELJ ENGEM TAP IN EKRANRA HA VEGE
totalT = Osszesen:
fossaT = FOSSA! Bitcoin ATM
satsT = SATS
forT = SZAMARA
fiatT = FIAT!
feedT = etess meg fiatot
chargeT = % toltes
printingT = Nyomtatas
waitT = kerlek varj
workingT = Munkalkodik...
thisVoucherT = Ez a voucher bevalthato
ofBitcoinT = Bitcoin ertekere
thankYouT = Koszonom
scanMeClaimT = Szkenneld meg egy Lightning tarcaval hogy megkapd a Bitcoinod
tooMuchFiatT = Tul sok FIAT!
contactOwnerT = Kerlek lepj kapcsolatba a tulajdonossal
failedT = HIBAS
unableT = nem sikerult beolvasni az lnurl
maxaT = FIGYELEM: max osszeg
willT = Alapertelmezett ertek lesz hasznalva
loadT = FIGYELEM: toltési arany
maxrT = FIGYELEM: max visszaallitas
printY = FIGYELEM: nyomtatas bool
langT = FIGYELEM: nyelvi hiba
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

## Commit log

2023-01-19 Added WT32-SC01 case
    [WT32-SC01 Case.stl]
2023-01-19 Added NV10 manual with host cable wiring diagram for DIY host programming cable build
2024-07-01 Work on printer
2024-07-02 Working receipt printer!
2024-07-02 NOw all connected devices work!
2024-07-02 Switched printer to use software serial and it works!
2024-07-02 Added esp software serial and thermal printer libraries
2024-07-03 bug fix on total printed on receipt
2024-07-03 Added PCB
    [Fossa PCB.kicad_pcb, Fossa PCB.kicad_sch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]
2024-07-03 Update receipt printing message position
2024-07-03 Updated screen layout code and credited Leigh for QR printing code in README
2024-07-08 Added Wiring diagram and organised docs a bit
    [Fossa PCB.kicad_pcb, Fossa PCB.kicad_sch, WT32-SC01 Case.stl]
2024-07-08 Removed old stls and added new PCB enclosure
    [WT32-SC01 enclosure lower.stl, WT32-SC01 enclosure upper.stl]
2024-07-08 Updated bill acceptor wiring diagram
2024-07-08 Move nv10 wiring table into markdown
2024-07-08 Clarify pin number not GPIO number on nv10 table in readme
2024-07-15 Corrected 12v and GND labels on board
    [Fossa PCB.kicad_pcb]
2024-07-21 Draft FOSSA Facia & Slot cover
    More coming soon. Will be amending for clearance with the screen.
    [FOSSA ATM Facia.stl, FOSSA ATM Slot Cover.stl]
2024-07-22 Prototype back box
    This is a prototype backbox for the FOSSA ATM.
    [FOSSA ATM Back Box.stl]
2024-07-22 Removed top-left pillar
    The top left pillar would clash with the top left bolt pruding out of the back of the coin acceptor so have removed.
    [FOSSA ATM Back Box.stl]
2024-07-23 Screen mount test added
    This uses the same sketch.
    [FOSSA ATM Screen Mount Test.stl]
2024-07-23 Updated the ATM Facia
    - Additional mounting holes at the back for an optional solenoid lock
    - Additional mounting holes for a 1591L proto board or 2 Channel Relay Breakout for the solenoid lock
    - Added more clearance for the WT32-SC01
    - Additional cooling vent for the WT32-SC01
    - Added more clearance to the 16-pin connectors on the WT32-SC01
    - Small adjustments made to the rounding and dimensions of the cash and coin acceptors
    [FOSSA ATM Facia.stl]
2024-07-24 Removed support that clashes with cash acceptor
    The triangular brace on the side clashed slightly with the cash acceptor so have removed it.
    [FOSSA ATM Back Box.stl]
2024-07-24 Reference model of the WT32-SC01 ESP32
2024-07-24 Update README.md
    Added bill of materials with links and details on 3D printing.
2024-07-25 Update README.md
    Added additional Arduino and LNBits instructions.
2024-07-25 Update README.md
    Added pictures and more details to the 3D print.
2024-07-25 Update README.md
    Minor text changes to the programming cable section to be more clear.
2024-07-26 Door added
    This is the door. You will also need the lever shim to affix to the inside of the case.
    [FOSSA ATM Door.stl]
2024-07-26 3mm and 4mm door lock lever shims
    [FOSSA ATM 3mm Lock Lever Shim.stl, FOSSA ATM 4mm Lock Lever Shim.stl]
2024-07-30 Updated models
    Lots of various amendments.
    [FOSSA ATM Backbox Note Holder.stl, FOSSA ATM Backbox.stl, FOSSA ATM Front Facia.stl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]
2024-07-30 Update README.md
    3D print specifics.
2024-08-01 Update README.md
    Updated printer settings.
2024-08-01 Added LNBits board cover
    [FOSSA ATM LNBits Board Cover.stl]
2024-08-14 Added if for if printer doesnt exist
2024-09-24 fix: ben's tweaks
    tweaksss
    fixing coin
    tweaks
    [100_config.ino, 102_helpers.ino, fossa.ino]
2024-10-05 fix: build was broken (#16)
    [100_config.ino]
2024-10-05 clear screen after error displays (#17)
    [100_config.ino]
2024-10-05 Removed print error
2024-10-05 stray print
2024-10-10 Fixed print er and printer test file
    [fossa.ino, testprint.ino]
